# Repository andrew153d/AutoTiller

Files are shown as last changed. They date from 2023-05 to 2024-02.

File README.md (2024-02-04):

# AutoTiller
An autopilot for my 1977 AMF Sunfish

## Usage ## 
- The AutoTiller attaches to the tiller handle with clips going to each side of the boat.

| Keypress | Action |
|---|---|
|  Set |  sets heading |
|+15|heading+=15|
|-15|heading-=15|
|+1|heaing++|
|-1|heading--|
|Fn & Set| Calibrates compass, rotate device around for 30 seconds|
|Fn & +1| deadspace++|
|Fn & +15| torquePID.P++|
|Fn & -1| deadspace--|
|Fn & -15| torquePID.P-- |

## Schematic

The schematic for the PCB can be found in the `media` directory:

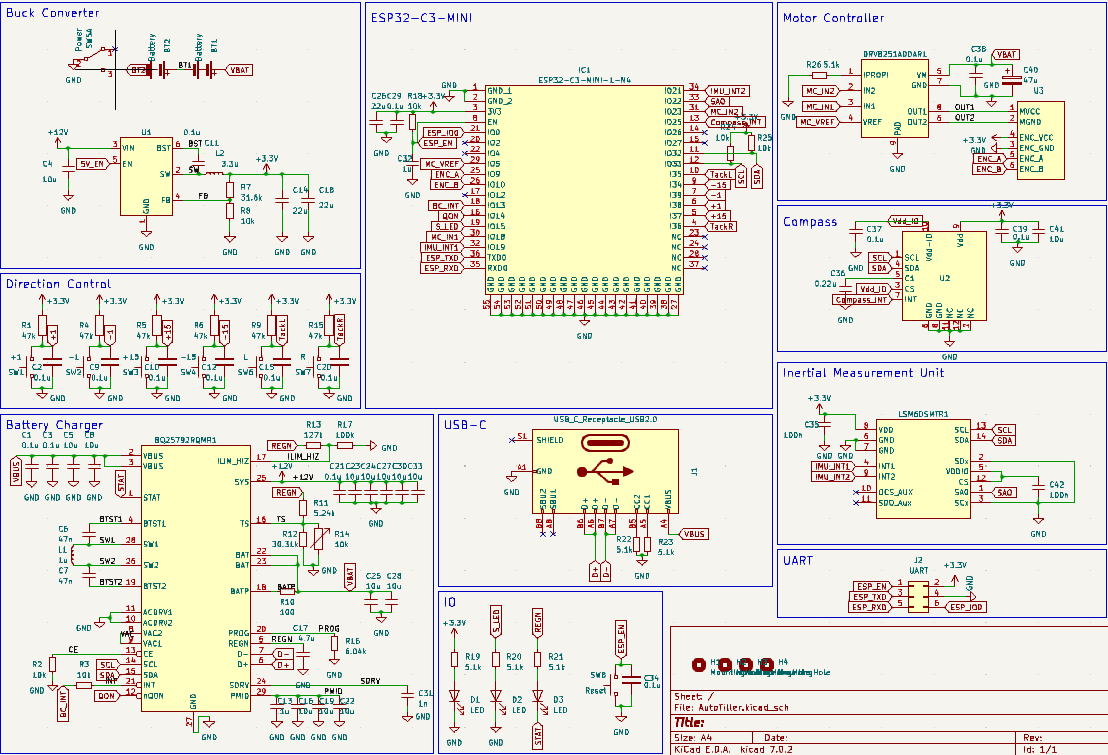
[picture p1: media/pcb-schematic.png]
PCB Schematic


## PCB Layout

The PCB layout file can also be found in the `media` directory:

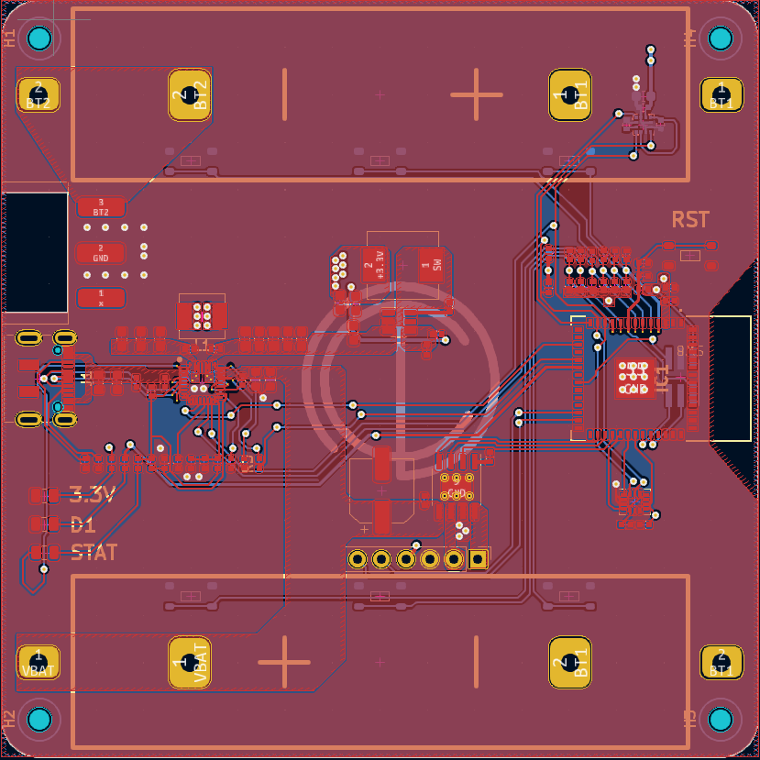
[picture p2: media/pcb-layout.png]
PCB Layout
 

## PCB Top Layer

The view of the board from the cockpit:

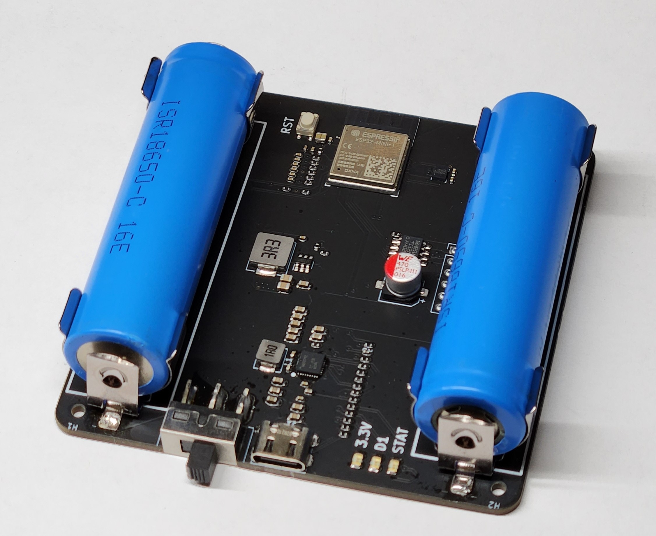
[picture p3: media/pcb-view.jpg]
PCB View


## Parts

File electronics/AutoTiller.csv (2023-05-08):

Source: | C:\Users\Andre\Documents\AutoTiller\AutoTillrt\AutoTiller\AutoTiller.kicad_sch
Date: | 4/28/2023 2:17:52 PM
Tool: | Eeschema (7.0.0)
Generator: | C:\Program Files\KiCad\7.0\bin\scripting\plugins/bom_csv_grouped_by_value.py
Component Count: | 86
Collated Components:
Item | Qty | Reference(s) | Value | LibPart | Footprint | Datasheet | DNP | Height | Manufacturer_Name | Manufacturer_Part_Number | Mouser Part Number | Mouser Price/Stock
1 | 1 | BQ25792RQMR1 | ~ | LiPo_Charger_BQ25792RQMR:BQ25792RQMR
2 | 1 | BT1 | Battery | Device:Battery |  | ~
3 | 11 | C1, C2, C6, C7, C24, C25, C26, C28, C29, C31, C33 | 10u | Device:C_Small |  | ~
4 | 4 | C3, C5, C23, C30 | 0.1u | Device:C_Small |  | ~
5 | 7 | C4, C10, C13, C14, C19, C22, C34 | 0.1u | Device:C | Capacitor_SMD:C_0402_1005Metric | ~
6 | 1 | C8 | 47n | Device:C_Small |  | ~
7 | 1 | C9 | 47nF | Device:C_Small |  | ~
8 | 2 | C11, C12 | 100n | Device:C_Small |  | ~
9 | 5 | C15, C16, C17, C18, C27 | 22u | Device:C_Small |  | ~
10 | 1 | C20 | 1n | Device:C_Small |  | ~
11 | 1 | C21 | 4.7u | Device:C_Small |  | ~
12 | 1 | C32 | 1u | Device:C_Small |  | ~
13 | 1 | C35 | 100 nF | Device:C_Small |  | ~
14 | 1 | C36 | 2.2uF | Device:C_Small |  | ~
15 | 1 | C37 | 0.1uF | Device:C_Small |  | ~
16 | 1 | C38 | 47uF | Device:C_Small |  | ~
17 | 1 | C39 | 100nF | Device:C_Small |  | ~
18 | 3 | D1, D2, D3 | LED | Device:LED |  | ~
19 | 1 | DRV8251ADDAR1 | ~ | DRV8251ADDAR:DRV8251ADDAR
20 | 1 | IC1 | ESP32-C3-MINI-1-N4 | ESP32-C3-MINI-1-N4:ESP32-C3-MINI-1-N4 | ESP32C3MINI1N4 | https://www.mouser.com/datasheet/2/891/Espressif_ESP32_C3_MINI_1_Datasheet-2006822.pdf |  |  | 2.55 | Espressif Systems | ESP32-C3-MINI-1-N4 | 356-ESP32-C3-MINI1N4 | https://www.mouser.co.uk/ProductDetail/Espressif-Systems/ESP32-C3-MINI-1-N4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
21 | 1 | J1 | USB_C_Receptacle | Connector:USB_C_Receptacle |  | https://www.usb.org/sites/default/files/documents/usb_type-c.zip
22 | 1 | J2 | UART | Connector_Generic:Conn_02x03_Odd_Even | Connector_PinHeader_1.27mm:PinHeader_2x03_P1.27mm_Vertical_SMD | ~
23 | 1 | L1 | 1u | Device:L_Small |  | ~
24 | 1 | L2 | 4.7u | Device:L_Small |  | ~
25 | 1 | L3 | 3.3u | Device:L_Small |  | ~
26 | 1 | LSM6DSMTR1 | ~ | LSM6DSMTR_IMU:LSM6DSMTR
27 | 1 | MMC5603NJ1 | ~ | MMC5603NJ_Compass:MMC5603NJ
28 | 6 | R1, R2, R3, R8, R9, R15 | 47k | Device:R | Resistor_SMD:R_0402_1005Metric | ~
29 | 1 | R4 | 52.3k | Device:R_Small |  | ~
30 | 5 | R5, R7, R17, R21, R22 | 10k | Device:R_Small |  | ~
31 | 1 | R6 | 31.6 | Device:R_Small |  | ~
32 | 1 | R10 | R_Small | Device:R_Small |  | ~
33 | 1 | R11 | 5.24k | Device:R_Small |  | ~
34 | 1 | R12 | 30.31k | Device:R_Small |  | ~
35 | 1 | R13 | 127k | Device:R_Small |  | ~
36 | 1 | R14 | 10k | Device:R_Variable |  | ~
37 | 1 | R16 | 100k | Device:R_Small |  | ~
38 | 4 | R18, R19, R20, R23 | 5.1k | Device:R_Small |  | ~
39 | 1 | SW1 | +1 | Switch:SW_Push | Push_Button:button_RKB2SJK250SMTR LFS | ~
40 | 1 | SW2 | -1 | Switch:SW_Push | Push_Button:button_RKB2SJK250SMTR LFS | ~
41 | 1 | SW3 | +15 | Switch:SW_Push | Push_Button:button_RKB2SJK250SMTR LFS | ~
42 | 1 | SW4 | -15 | Switch:SW_Push | Push_Button:button_RKB2SJK250SMTR LFS | ~
43 | 1 | SW5 | L | Switch:SW_Push | Push_Button:button_RKB2SJK250SMTR LFS | ~
44 | 1 | SW6 | R | Switch:SW_Push | Push_Button:button_RKB2SJK250SMTR LFS | ~
45 | 1 | SW7 | Reset | Switch:SW_Push | Push_Button:button_RKB2SJK250SMTR LFS | ~
46 | 2 | U1, U2 | ~ | Buck_Converter_AP62200TWU-7:AP62200TWU-7
47 | 1 | U3 | ~ | Encoder_Motor:Motor

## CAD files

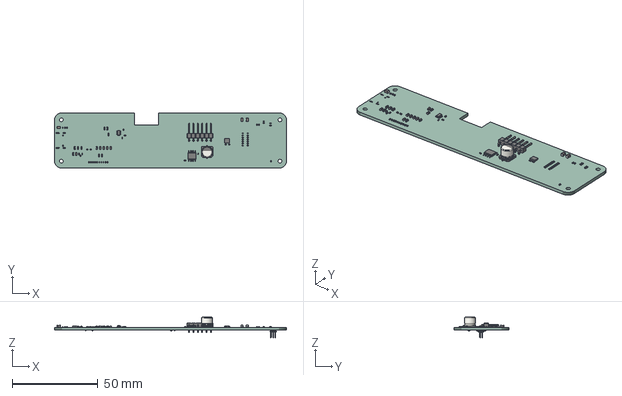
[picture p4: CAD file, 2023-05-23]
electronics/AutoTiller.step
135.0 x 32.0 x 12.0 mm
PCB

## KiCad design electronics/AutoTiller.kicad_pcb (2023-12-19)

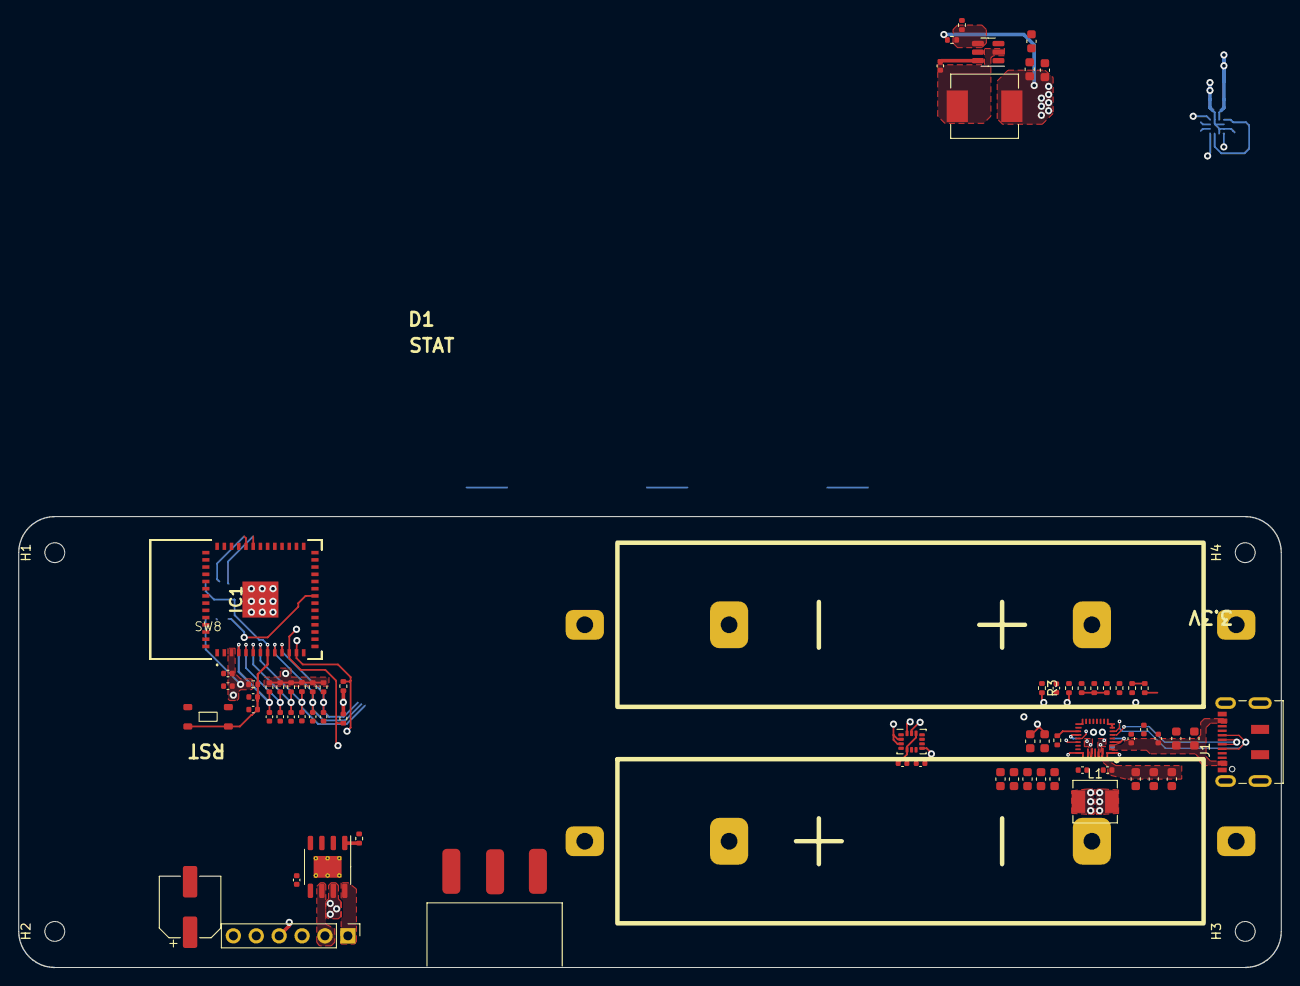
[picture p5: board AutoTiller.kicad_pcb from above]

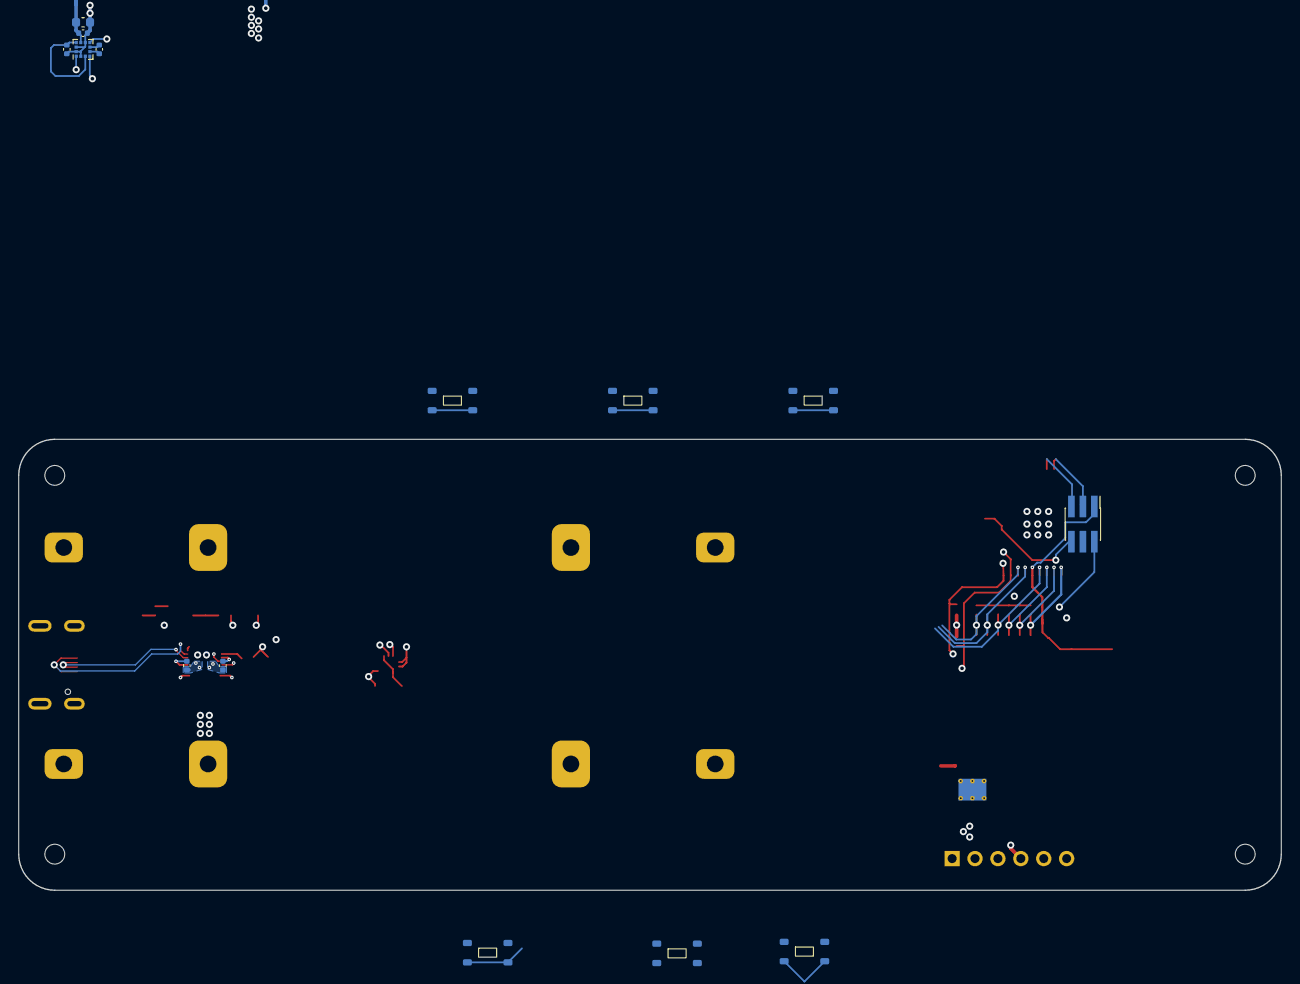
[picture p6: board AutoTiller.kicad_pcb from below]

Board: 4 copper layers, 140.0 x 50.0 mm, 88 parts (14 on the bottom side), 55 nets.

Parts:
BQ25792RQMR1: BQ25792
BT1, BT2: Battery; 254 clip
C1, C2, C3, C9, C10, C11, C12, C15, C20, C21, C29, C34, C37, C38, C39: 0.1u; C_0402_1005Metric
C4, C5, C8, C16, C19, C22, C23, C24, C25, C27, C28, C30, C33, C41: 10u; C_0603_1608Metric
C6, C7: 47n; C_0402_1005Metric
C13: .1u; C_0402_1005Metric
C14, C18: 22u; C_0603_1608Metric
C17: 4.7u; C_0402_1005Metric
C26: 22u; C_0402_1005Metric
C31: 1n; C_0402_1005Metric
C32: 1u; C_0402_1005Metric
C35, C42: 100n; C_0402_1005Metric
C36: 0.22u; C_0402_1005Metric
C40: 47u; CP_Elec_6.3x5.9
DRV8251ADDAR1: HSOP-8-1EP_3.9x4.9mm_P1.27mm_EP2.41x3.1mm_ThermalVias
H1, H2, H3, H4: MountingHole; MountingHole_2.2mm_M2
IC1: ESP32-C3-MINI-1-N4; ESP32MINI1N4
J1: USB_C_Receptacle_USB2.0; USB_C_Receptacle_JAE_DX07S016JA1R1500
J2: UART; PinHeader_2x03_P1.27mm_Vertical_SMD
L1: 1u; L_Sunlord_MWSA0402S
L2: 3.3u; L_Sunlord_MWSA0618S
LSM6DSMTR1: LGA-14_3x2.5mm_P0.5mm_LayoutBorder3x4y
R1, R4, R5, R6, R9, R15: 47k; R_0402_1005Metric
R2, R3, R8, R14, R18, R24, R25: 10k; R_0402_1005Metric
R7: 31.6k; R_0402_1005Metric
R10: 100; R_0402_1005Metric
R11: 5.24k; R_0402_1005Metric
R12: 30.31k; R_0402_1005Metric
R13: 127k; R_0402_1005Metric
R16: 6.04k; R_0402_1005Metric
R17: 100k; R_0402_1005Metric
R26: 5.1k; R_0402_1005Metric
SW1: +1; Tactile_5.5mmx2.85mm
SW2: -1; Tactile_5.5mmx2.85mm
SW3: +15; Tactile_5.5mmx2.85mm
SW4: -15; Tactile_5.5mmx2.85mm
SW5: Power; 0.5in_Slide
SW6: L; Tactile_5.5mmx2.85mm
SW7: R; Tactile_5.5mmx2.85mm
SW8: Reset; Tactile_5.5mmx2.85mm
U1: TSOT-23-6
U2: LGA-12_2x2mm_P0.5mm
U3: PinHeader_1x06_P2.54mm_Vertical

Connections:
+1: C2.1, IC1.6 (I38), R1.2, SW1.2
+3.3V: C14.1, C18.1, C26.1, C29.1, C35.1, C39.1, C41.1, IC1.3 (3V3), J2.2, L2.2, LSM6DSMTR1.8 (VDD), R1.1, R4.1, R5.1, R6.1, R7.1, R9.1, R15.1, R18.1, R24.1, R25.1, U2.9 (Vdd), U3.4 (ENC_VCC)
+12V: BQ25792RQMR1.25 (SYS), C4.1, C21.1, C23.1, C24.1, C27.1, C30.1, C33.1, U1.3 (VIN)
+15: C10.1, IC1.5 (I37), R5.2, SW3.2
-1: C9.1, IC1.7 (I39), R4.2, SW2.2
-15: C12.1, IC1.9 (I34), R6.2, SW4.2
/BATP: BQ25792RQMR1.18 (BATP), R10.1
/BST: C11.1, U1.6 (BST)
/BT1: BT1.2 (-), BT2.1 (+)
/BTST1: BQ25792RQMR1.4 (BTST1), C6.1
/BTST2: BQ25792RQMR1.19 (BTST2), C7.2
/CE: BQ25792RQMR1.13 (CE), R2.2
/FB: R7.2, R8.1, U1.4 (FB)
/ILIM_HIZ: BQ25792RQMR1.17 (ILIM_HIZ), R13.1, R17.1
/INT: BQ25792RQMR1.21 (INT), R3.2
/OUT1: DRV8251ADDAR1.8 (OUT1), U3.1 (MVCC)
/OUT2: DRV8251ADDAR1.6 (OUT2), U3.2 (MGND)
/PMID: BQ25792RQMR1.29 (PMID), C13.1, C16.1, C19.1, C22.1
/PROG: BQ25792RQMR1.20 (PROG), R16.1
/SDRV: BQ25792RQMR1.24 (SDRV), C31.1
/SW: C11.2, L2.1, U1.2 (SW)
/SW1: BQ25792RQMR1.28 (SW1), C6.2, L1.2
/SW2: BQ25792RQMR1.26 (SW2), C7.1, L1.1
/TS: BQ25792RQMR1.16 (TS), R11.2, R12.1, R14.1
/VAC: BQ25792RQMR1.8 (VAC2), BQ25792RQMR1.9 (VAC1)
BC_INT: IC1.18 (IO13), R3.1
BT2: BT2.2 (-), SW5.3 (C)
Compass_INT: IC1.13 (IO25), U2.7 (INT)
D+: BQ25792RQMR1.6 (D+), J1.A6 (D+), J1.B6 (D+)
D-: BQ25792RQMR1.7 (D-), J1.A7 (D-), J1.B7 (D-)
ENC_A: IC1.25 (IO9), U3.5 (ENC_A)
ENC_B: IC1.26 (IO10), U3.6 (ENC_B)
ESP_EN: C32.1, C34.1, IC1.8 (EN), J2.1, R18.2, SW8.2
ESP_IO0: IC1.21 (IO0), J2.6
ESP_RXD: IC1.35 (RXD0), J2.5
ESP_TXD: IC1.36 (TXD0), J2.3
GND: BQ25792RQMR1.10 (ACDRV2), BQ25792RQMR1.11 (ACDRV1), BQ25792RQMR1.27 (GND), C1.2, C2.2, C3.2, C4.2, C5.2, C8.2, C9.2, C10.2, C12.2, C13.2, C14.2, C15.2, C16.2, C17.2, C18.2, C19.2, C20.2, C21.2, C22.2, C23.2, C24.2, C25.2, C26.2, C27.2, C28.2, C29.2, C30.2, C31.2, C32.2, C33.2, C34.2, C35.2, C36.2, C37.2, C38.2, C39.2, C40.2, C41.2, C42.2, DRV8251ADDAR1.7 (GND), DRV8251ADDAR1.9 (PAD), IC1.1 (GND_1), IC1.2 (GND_2), IC1.27 (GND), IC1.38 (GND), IC1.39 (GND), IC1.40 (GND), IC1.41 (GND), IC1.42 (GND), IC1.43 (GND), IC1.44 (GND), IC1.45 (GND), IC1.46 (GND), IC1.47 (GND), IC1.48 (GND), IC1.49 (GND), IC1.50 (GND), IC1.51 (GND), IC1.52 (GND), IC1.53 (GND), IC1.54 (GND), IC1.55 (GND), J1.A1 (GND), J1.A12 (GND), J1.B1 (GND), J1.B12 (GND), J2.4, LSM6DSMTR1.2 (SDx), LSM6DSMTR1.3 (SCx), LSM6DSMTR1.6 (GND), LSM6DSMTR1.7 (GND), R2.1, R8.2, R12.2, R14.2, R16.2, R17.2, R26.1, SW1.1, SW2.1, SW3.1, SW4.1, SW5.2 (B), SW6.1, SW7.1, SW8.1, U1.1 (GND), U2.2 (NC), U2.6 (GND), U2.8 (GND), U2.11 (NC), U2.12 (NC), U3.3 (ENC_GND)
IMU_INT1: IC1.32 (IO19), LSM6DSMTR1.4 (INT1)
IMU_INT2: IC1.34 (IO21), LSM6DSMTR1.9 (INT2)
MC_IN1: DRV8251ADDAR1.3 (IN1), IC1.30 (IO18)
MC_IN2: DRV8251ADDAR1.2 (IN2), IC1.31 (IO23)
MC_VREF: DRV8251ADDAR1.4 (VREF), IC1.29 (IO5)
unnamed: DRV8251ADDAR1.1 (IPROPI), R26.2
unnamed: C42.1, LSM6DSMTR1.5 (VDDIO), LSM6DSMTR1.12 (CS)
unnamed: C36.1, U2.5 (C1)
QON: BQ25792RQMR1.12 (nQON), IC1.16 (IO14)
REGN: BQ25792RQMR1.5 (REGN), C17.1, R11.1, R13.2
SAO: IC1.33 (IO22), LSM6DSMTR1.1 (SA0)
SCL: BQ25792RQMR1.14 (SCL), IC1.12 (IO33), LSM6DSMTR1.13 (SCL), R24.2, U2.1 (SCL)
SDA: BQ25792RQMR1.15 (SDA), IC1.11 (IO32), LSM6DSMTR1.14 (SDA), R25.2, U2.4 (SDA)
TackL: C15.1, IC1.10 (I35), R9.2, SW6.2
TackR: C20.1, IC1.4 (I36), R15.2, SW7.2
VBAT: BQ25792RQMR1.22 (BAT), BQ25792RQMR1.23 (BAT), BT1.1 (+), C25.1, C28.1, C38.1, C40.1, DRV8251ADDAR1.5 (VM), R10.2
VBUS: BQ25792RQMR1.2 (VBUS), BQ25792RQMR1.3 (VBUS), C1.1, C3.1, C5.1, C8.1, J1.A4 (VBUS), J1.A9 (VBUS), J1.B4 (VBUS), J1.B9 (VBUS)
Vdd_IO: C37.1, U2.3 (CS), U2.10 (Vdd-IO)

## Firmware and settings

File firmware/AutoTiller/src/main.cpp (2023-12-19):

#include <Arduino.h>
#include "defines.h"
#include "Wire.h"
#include "BQ25792.h"
#include "LIS2MDL_Driver.h"
#include "pid.h"
#include "filter.h"
#include "utils.h"
#include "motorDriver.h"

// running average filter
#define AVG_LENGTH 50
float average_buf[AVG_LENGTH];
int8_t avg_index = 0;
float average(float input);

float deadspace = 0;
PIDController anglePID(2, 0, 0, 2, 10);

long printTimer = 0;
typedef struct
{
  bool Set;
  bool Function;
  bool m1;
  bool p1;
  bool m15;
  bool p15;
} inputButtons;
inputButtons buttonPressed, lastButtonPressed;

enum Mode
{
  AUTOPILOT_OFF,
  AUTOPILOT_ON
} AutopilotMode;

// global variables
float targetHeading = 0;
int nowTime;
int dummy = 0;
uint8_t channel = 13;

// Connected Devices
BQ25792 charger(0, 0);
LIS2MDL compass;
motorManager motor;

void setMotor(int vref);
void testMotor();
float average(float input);
void updateButtons();
void task();
float getCompassError(float targetHeading, float currentHeading);

void IRAM_ATTR ISR()
{
  motor.handleInturrupt();
}

void setup()
{

  DEBUG_BEGIN(115200);

  Wire.begin(SDA_PIN, SCL_PIN);

  // set pinModes
  pinMode(STAT_LED, OUTPUT);
  pinMode(FUNCTION, INPUT);
  pinMode(SET, INPUT);
  pinMode(PIN_m15, INPUT);
  pinMode(PIN_m1, INPUT);
  pinMode(PIN_p15, INPUT);
  pinMode(PIN_p1, INPUT);
  pinMode(MOTOR_DIR_2, OUTPUT);
  pinMode(MOTOR_DIR_1, OUTPUT);
  pinMode(ENC_A, INPUT);
  pinMode(ENC_B, INPUT);
  pinMode(COMPASSDATAREADY, INPUT);

  // start Charger
  charger.reset();
  delay(500); // give the charger time to reboot
  charger.flashChargeLevel(STAT_LED);

  if (compass.begin())
  {
    DEBUG_PRINTLN("Compass Found");
  }
  else
  {
    DEBUG_PRINTLN("Failed to find sensor");
    while (1)
    {
    };
  }

  attachInterrupt(ENC_A, ISR, FALLING);
  int16_t Xofst = -69;
  int16_t Yofst = -438;
  compass.writeXOffset(Xofst);
  compass.writeYOffset(Yofst);
  compass.enableAvgFilter();
  compass.filter_alpha = 0.02;
  motor.begin();
}

void loop()
{
  nowTime = millis();

  updateButtons(); // update the state of the buttons
  task();
}

void task()
{

  if (buttonPressed.Set && !lastButtonPressed.Set)
  {
    if (!buttonPressed.Function)
    {
      if (AutopilotMode == AUTOPILOT_ON)
      {
        AutopilotMode = AUTOPILOT_OFF;
        DEBUG_PRINTLN("AutoPilot Off");
      }
      else if (AutopilotMode == AUTOPILOT_OFF)
      {
        AutopilotMode = AUTOPILOT_ON;
        targetHeading = compass.getHeading();
        DEBUG_PRINTF("Target heading: %.1f\t", targetHeading);
        DEBUG_PRINTLN("AutoPilot On");
      }
    }
    else
    {
      DEBUG_PRINTLN("Start Calibrating");
      DEBUG_PRINTF("Old Values %.1d%5.1d\n", compass.readXOffset(), compass.readYOffset());
      compass.calibrate();
      DEBUG_PRINTF("New Values %.1d%5.1d\n", compass.readXOffset(), compass.readYOffset());
      DEBUG_PRINTLN("Done Calibrating");
    }
  }
  else if (buttonPressed.p1 && !lastButtonPressed.p1)
  {
    if (!buttonPressed.Function)
    {
      targetHeading--;
      DEBUG_PRINT("New Heading: ");
      DEBUG_PRINTLN(targetHeading);
    }
    else
    {
      anglePID.output_ramp++;
      DEBUG_PRINT("New ramp: ");
      DEBUG_PRINTLN(anglePID.output_ramp);
    }
  }
  else if (buttonPressed.p15 && !lastButtonPressed.p15)
  {
    if (!buttonPressed.Function)
    {
      targetHeading -= 15;
      DEBUG_PRINT("New Heading: ");
      DEBUG_PRINTLN(targetHeading);
    }
    else
    {
      anglePID.P += .1;
      DEBUG_PRINT("New P: ");
      DEBUG_PRINTLN(anglePID.P);
    }
  }
  else if (buttonPressed.m1 && !lastButtonPressed.m1)
  {
    if (!buttonPressed.Function)
    {
      targetHeading++;
      DEBUG_PRINT("New Heading: ");
      DEBUG_PRINTLN(targetHeading);
    }
    else
    {
      anglePID.output_ramp--;
      if (deadspace < 0)
        deadspace = 0;
      DEBUG_PRINT("New ramp: ");
      DEBUG_PRINTLN(anglePID.output_ramp);
    }
  }
  else if (buttonPressed.m15 && !lastButtonPressed.m15)
  {
    if (!buttonPressed.Function)
    {
      targetHeading += 15;
      DEBUG_PRINT("New Heading: ");
      DEBUG_PRINTLN(targetHeading);
    }
    else
    {
      anglePID.P -= .1;
      DEBUG_PRINT("New P: ");
      DEBUG_PRINTLN(anglePID.P);
    }
  }

  if (AutopilotMode == AUTOPILOT_ON)
  {
    float tillerHeading = average(compass.getHeading());
    float tillerAngleToHull = motor.getTillerAngleToHull();
    float hullHeading = tillerHeading + tillerAngleToHull;
    float Error = getCompassError(targetHeading, hullHeading);
    float targetAngle = anglePID(Error);
    motor.setTargetTillerAngle(targetAngle);
    motor.task();
    // if (everyXms(&printTimer, 500))
    ///{7622
    // DEBUG_PRINTF("Tiller Heading %.1f TillerAngleToHull %.1f  Hull Heading %.1f  Error %.1f  TargetTillerAngle %.1f  MotorTorque %.1f\n", tillerHeading, tillerAngleToHull, hullHeading, Error, targetAngle, motor.motorTorque);
    DEBUG_PRINTF("%8.1f%8.1f%8.1f%8.1f%8.1f%8.1f\n", tillerHeading, tillerAngleToHull, hullHeading, Error, targetAngle, motor.motorTorque);
    //}
  }
  else
  {
    motor.setMotor(0);
    if (buttonPressed.Function)
    {
      DEBUG_PRINTLN(average(compass.getHeading()));
    }
  }
}

void updateButtons()
{
  lastButtonPressed = buttonPressed;
  buttonPressed.Function = !digitalRead(FUNCTION);
  buttonPressed.Set = !digitalRead(SET);
  buttonPressed.m15 = !digitalRead(PIN_m15);
  buttonPressed.m1 = !digitalRead(PIN_m1);
  buttonPressed.p1 = !digitalRead(PIN_p1);
  buttonPressed.p15 = !digitalRead(PIN_p15);
  digitalWrite(STAT_LED, (buttonPressed.Function || buttonPressed.m15 || buttonPressed.Set || buttonPressed.p15 || buttonPressed.m1 || buttonPressed.p1));
}

float getCompassError(float targetHeading, float currentHeading)
{
  float error = targetHeading - currentHeading;

  if (error > 180.0)
  {
    error -= 360.0;
  }
  else if (error < -180.0)
  {
    error += 360.0;
  }

  return ((abs(error) < deadspace) ? 0 : error);
}

float average(float input)
{

  avg_index++;
  avg_index = avg_index % AVG_LENGTH;
  average_buf[avg_index] = input;

  float min = 360;
  float max = 0;
  float sum = 0;
  for (float val : average_buf)
  {
    if (val < min)
      min = val;
    if (val > max)
      max = val;
    sum += val;
  }

  // DEBUG_PRINTF("Min: %f  Max: %f\n", min, max);
  return sum / AVG_LENGTH;
}

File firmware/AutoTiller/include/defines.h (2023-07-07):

// PIN definitions
#define IMU_ADDR_BIT7_PIN 22
#define SDA_PIN 32
#define SCL_PIN 33
#define FUNCTION 35
#define PIN_m15 37
#define PIN_m1 38
#define PIN_p1 39
#define PIN_p15 34
#define SET 36
#define STAT_LED 15
#define MOTOR_DIR_1 18
#define MOTOR_DIR_2 23
#define MOTOR_VREF 5
#define COMPASSDATAREADY 25
#define ENC_A 9
#define ENC_B 10

#define AVG_LENGTH 20

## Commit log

2023-05-08 Restructure and add README
    [AutoTiller-B_Cu.gbr, AutoTiller-B_Mask.gbr, AutoTiller-B_Paste.gbr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]
2023-05-08 add pcb view
2023-05-23 OTA working
    [AutoTiller-B_Cu.gbr, AutoTiller-B_Mask.gbr, AutoTiller-B_Paste.gbr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]
2023-05-29 Final Rev2 PCB
    [AutoTiller-B_Cu.gbr, AutoTiller-B_Mask.gbr, AutoTiller-B_Paste.gbr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]
2023-06-23 Simple PID controller working
2023-06-27 working simple pwm and inturrupt
2023-06-27 working inturrupts and pwm within motor class
2023-06-27 add light flashing for battery level output
2023-07-02 allow charger to flash battery level
